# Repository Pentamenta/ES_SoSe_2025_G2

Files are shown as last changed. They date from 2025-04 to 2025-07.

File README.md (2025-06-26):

# ES_SoSe_2025_G2
 Projekt zur Entwicklung eines automatisierten Fahrzeuges und eines Dashboards für den Kurs Embedded Systems 1 an der BHT Berlin.

## Workflow

### Git

Es wird mit Git gearbeitet.  
Vor jeder Arbeitsphase wird das Repository gepullt.
Gearbeitet wird nur in Branches, niemals direkt im Main. Es wird nur gemerged, wenn der Branch erfolgreich getestet wurde.
Vor dem Commit wird ein weiteres mal gepullt, um Mergefehler durch paralleles Arbeiten zu vermeiden.

## Hardware

Als Basis für beide Projektteile wird ein Arduino Nano BLE 33 verwendet. Das Auto verfügt zusätzlich über einen Arduino MEGA, da weitere Pins für die Steuerung der IOs benötigt wurden. Der Arduino Nano BLE 33 bleicht zentrale Anlaufstelle für die Drahtloskommunikation.

Um das Board Arduino Nano BLE 33 zu bespielen:
 1. Unter Werkzeuge --> Board --> Boardverwalter wählen
 2. Nach "Arduino Mbed OS Nano Boards" suchen und installieren
 3. Unter Board erscheint nun die neue Option "Arduino Mbed OS Nano Boards"
 4. Dort "Arduino Nano 33 BLE" wählen

## Software

### Bibliotheken (Fortlaufend zu erweitern)

Für das Projekt zu installierende Bibliotheken:
- ArduinoBLE
- U8g2 von olikraus (beim Inkludieren werden 3 Bibliotheken eingefügt, wir brauchen nur die U8g2lib)
- Arduino_BMI270_BMM150
- Adafruit_SSD1306
- Adafruit_GFX
- Wire
- Servo

### Softwarestruktur

Im Repository befinden sich zwei Ordner mit darin jeweils gleichnamigen Arduino Programmen.
- Code_ Dashboard --> Code_Dashboard.ino
- Code_Car_Connect --> Code_Car_Connect.ino
- Code_Car --> Code_Car.ino

In diesen Dateien wird programmiert. Ein Aufteilen in ausgelagerte .h Dateien ist erwünscht.  

In der externen Datei EBS_BLE.h werden Variablen für die BLE Kommunikation definiert, die in allen Programmen gleich seien müssen. Aufgrund von beschränkungen der Arduino IDE kann diese Datei nicht extern verlinkt werden, sondern muss in jedem Programmordner einzeln existieren. Es ist extrem wichtig, dass diese Dateien immer auf dem selben Stand sind.

### Coding

- Es ist soviel wir möglich über Funktionen zu lösen, um den Main loop so übersichtlich wie möglich zu halten.
- Delays und längere Loops sind zu vermeiden. Das Programm muss den Loop ständig durchlaufen, um die Drahtloskpommunikation nicht zu behindern.
- Der Code ist ausführlich zu kommentieren und am Ende der Kommentare der Name des bearbeiters hinzuzufügen, um Rückfragen zu vereinfachen. Es Reicht wenn der Namen einmal zu Begin einer Funktion notiert wird.

## BLE Documentation

Die Drahtlosverbindung zwischen Dashboard und Auto wird über Bluetooth Low Energy gelöst. 
Hierbei dient das Dashboard als Central Device und das Auto als Peripheral Device.

### Einführung BLE

- Das Peripherial Device ließt Daten vom Central Device aus
	- Darunter fallen sämtliche Anweisungen an das Auto, wie zu erreichende Geschwindigkeit und Lenkeinschlag
- Das Peripherial Device schreibt Daten andas Central Device.
	- Hiermit werden laufende Daten wie Sensor - Messwerte und Geschwindigkeit an das Dashboard übergeben.

### Datenstruktur BLE im Projekt

Datenübertragung mit BLE funktioniert über sogenannte Service.
Ein Central Device stellt eine Reihe von klar Definierten Service zur verfügung. 
Das Peripherial Device, welches diesen Service kennt, kann mit dem Central Device eine Verbindung aufbauen.
Service bestehen aus so genannten Charakteristiken, welche im Endeffekt einzelne Variablen sind.
Eine Gruppe aus Service nennt man Profil.

Jeder Service besitzt eine einzigartige UUID. Entdeckt ein Peripheral Device einen Service kann dieses, die darin enthaltenen Charakteristiken, lesen, beschreiben, oder überwachen.
Jede Charakteristik besitzt ebenfalls eine einzigartige UUID.

Die Uuids un dazugehörigen Charakteristika werden in der Datei "EBS_BLE.h" deklariert. Mittels bedigter Kompilierung werden Funktionen an den jeweiligen Code angepasst.

Die Tags für die bedingte Programmierung der einzelnen Programme lauten:
- Code_Dashboard.ino --> DASH
- Code_Car_Connect.ino --> CAR_CONNECT
- Code_Car.ino --> CAR

## Features

### Fahrzeug

- Blinker / Warnlicht
- Lenkung
	- Heckantrieb mit Servolenkung vorne
- Abstandssensor mit Buzzer
- Geschwindigkeitssensor
- Tempomat

### Dashboard

- Steuerung
	- Servolenkung über Joystick
	- Gas/Bremse über Joystick
- Tacho auf Bildschirm 
- Taster für Blinker, Tempomat, Scheinwerfer
- Bildschirme (1-3): Tachoanzeige, Parkanzeige, Tempomat Geschwindigkeit, Lüfter, Heizung

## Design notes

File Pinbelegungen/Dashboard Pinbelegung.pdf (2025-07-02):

Dashboard Pinbelegung

02.07.2025

Gerät | Pin | Pin Arduino | Pin Arduino | Pin | Gerät
LED ABS | Anode | D13 | D12 | Anode | LED Airbag
- | 3V3 | 3V3 | D11 | Anode | LED Tempomat
- | - | AREF | D10 | 1 | Taster Fernlicht
Joystick links Y | 4 | A0 | D09 | 1 | SDA Bildschirm links
Joystick links X | 3 | A1 | D08 | 2 | SCL Bildschirm links
Joystick rechts Y | 4 | A2 | D07 | 1 | Taster Scheinwerfer
Joystick rechts X | 3 | A3 | D06 | 1 | Taster Tempomat Set
SDA Display mitte / rechts | 1 / 1 | A4 | D05 | 1 | Taster Tempomat An / Aus
SCL Display mitte / rechts | 2 / 2 | A5 | D04 | Anode | LED BLE Connection
LED Blinker links | Anode | A6 | D03 | 5 | Taster Joystick rechts
LED Blinker rechts | Anode | A7 | D02 | 5 | Taster Joystick links
- | - | 5V | GND | GND | -
- | - | RESET | RESET | 1 | Taster Reset
- | GND | GND | D01 | - | -
Batteriespannung | + | VIN | D00 | - | -

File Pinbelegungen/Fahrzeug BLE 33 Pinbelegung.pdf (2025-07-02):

Fahrzeug BLE 33 Pinbelegung

02.07.2025

Gerät | Pin | Pin Arduino | Pin Arduino | Pin | Gerät
- | - | D13 | D12 | - | -
- | - | 3V3 | D11 | - | -
- | - | AREF | D10 | - | -
- | - | A0 | D09 | - | -
- | - | A1 | D08 | - | -
- | - | A2 | D07 | - | -
- | - | A3 | D06 | - | -
- | - | A4 | D05 | - | -
- | - | A5 | D04 | Anode | LED BLE Connection
- | - | A6 | D03 | - | -
- | - | A7 | D02 | D04 | Arduino MEGA
- | - | 5V | GND | GND | -
- | - | RESET | RESET | - | -
- | GND | GND | D01 | D19 | Arduino MEGA Rx1
Batteriespannung | + | VIN | D00 | D18 | Arduino MEGA Tx1

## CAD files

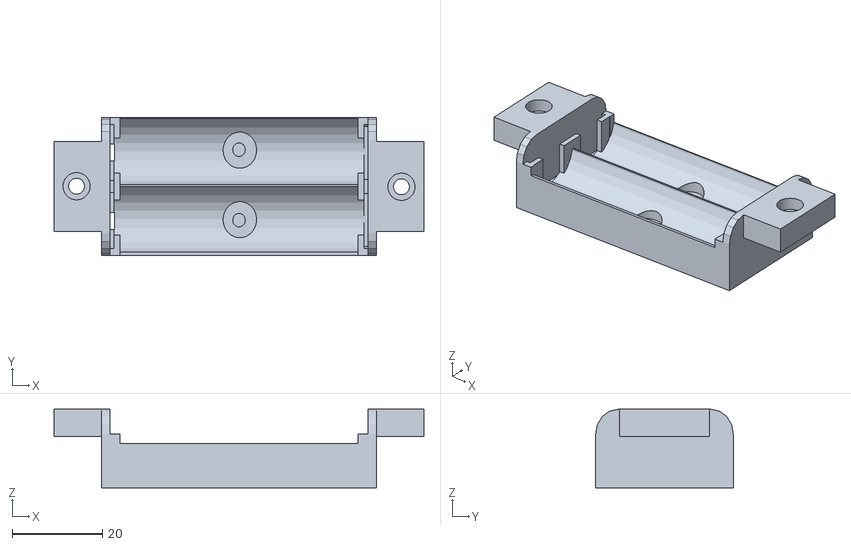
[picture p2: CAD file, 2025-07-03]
3D-Objekte/arduino 4WD controller battery holder.stl
82.0 x 30.5 x 17.4

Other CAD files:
3D-Objekte/lower_prt.prt
3D-Objekte/upper_prt.prt

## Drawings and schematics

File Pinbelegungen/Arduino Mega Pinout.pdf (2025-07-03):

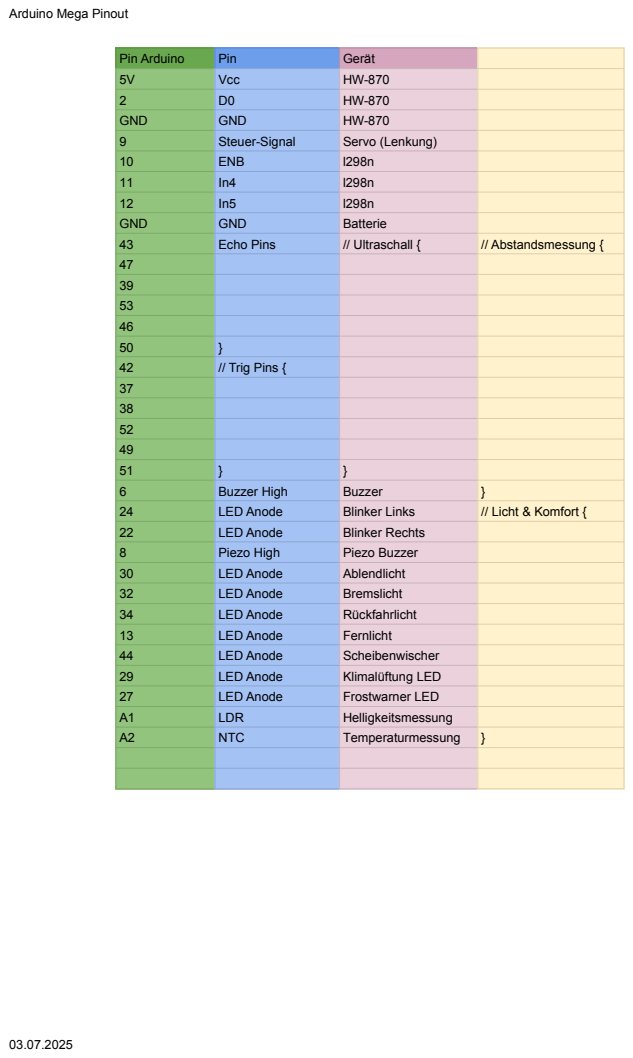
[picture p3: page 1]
Pin Arduino; Pin; Gerät; Vcc; GND; Steuer-Signal; Servo (Lenkung); ENB; Batterie; Echo Pins; // Ultraschall {; // Abstandsmessung {; // Trig Pins {; Buzzer High; Buzzer; LED Anode; Blinker Links; // Licht & Komfort {; Blinker Rechts; Piezo High; Piezo Buzzer; Ablendlicht; Bremslicht; Rückfahrlicht; Fernlicht; Scheibenwischer; Klimalüftung LED; Frostwarner LED; LDR; Helligkeitsmessung; NTC; Temperaturmessung

Arduino Mega Pinout

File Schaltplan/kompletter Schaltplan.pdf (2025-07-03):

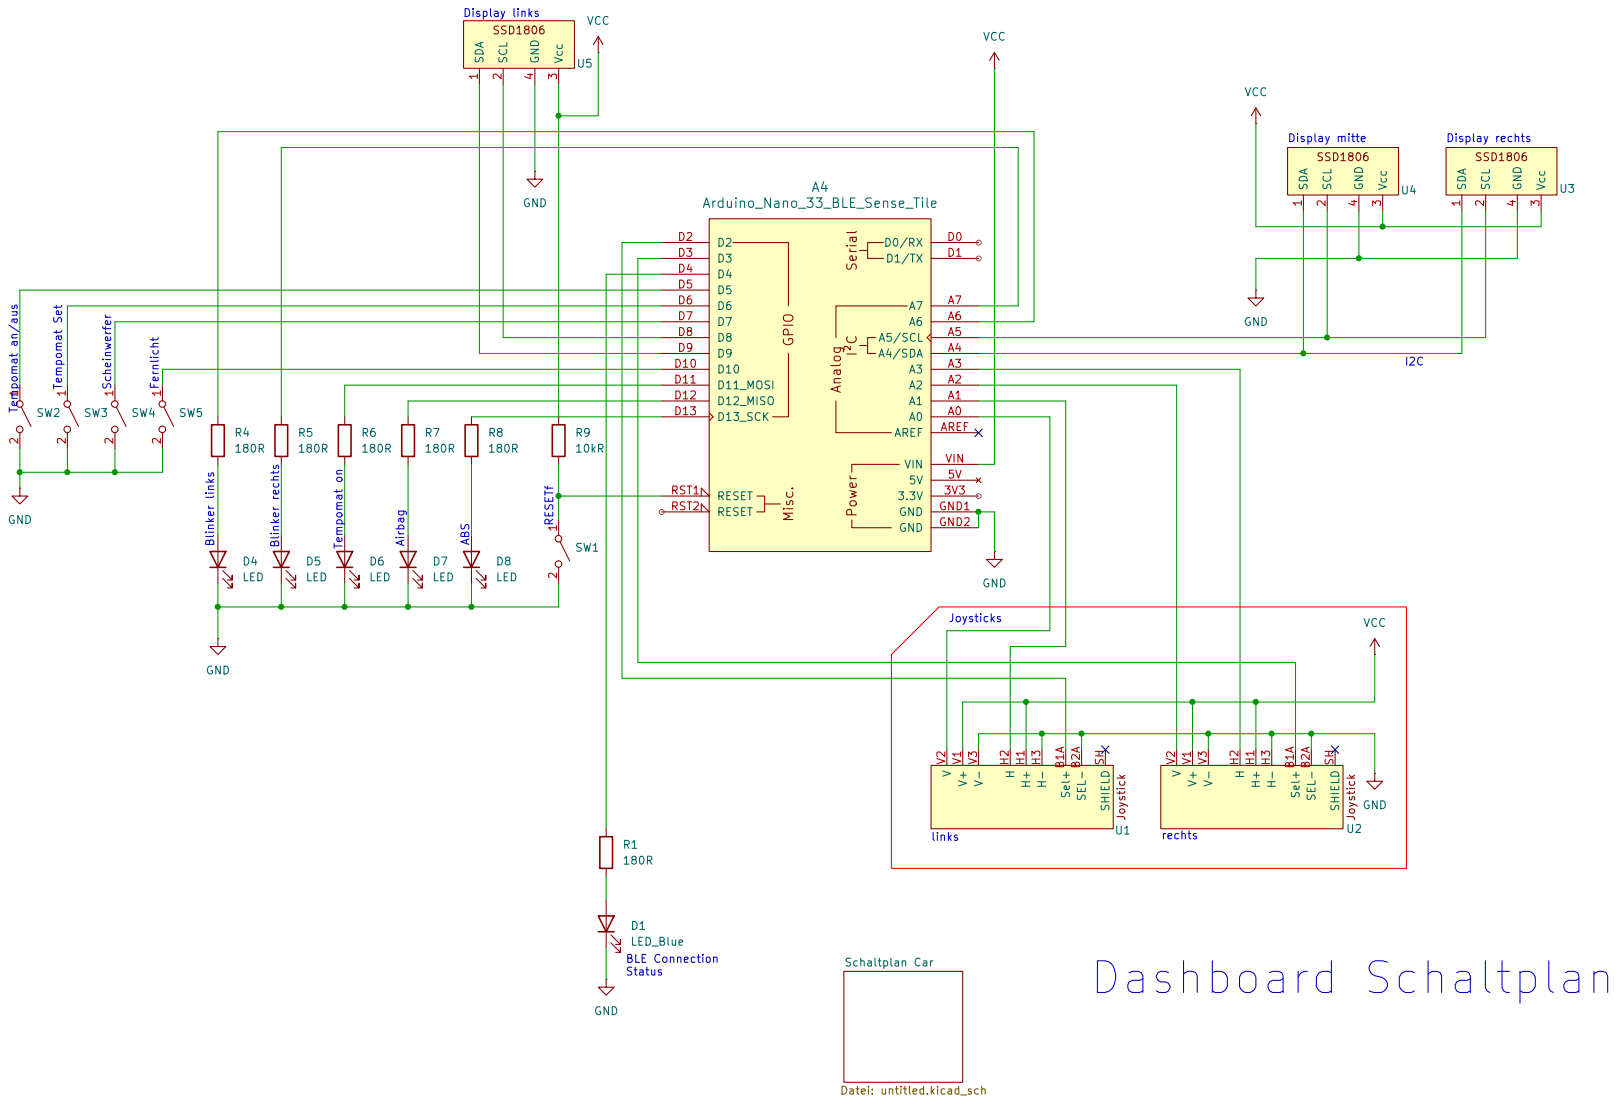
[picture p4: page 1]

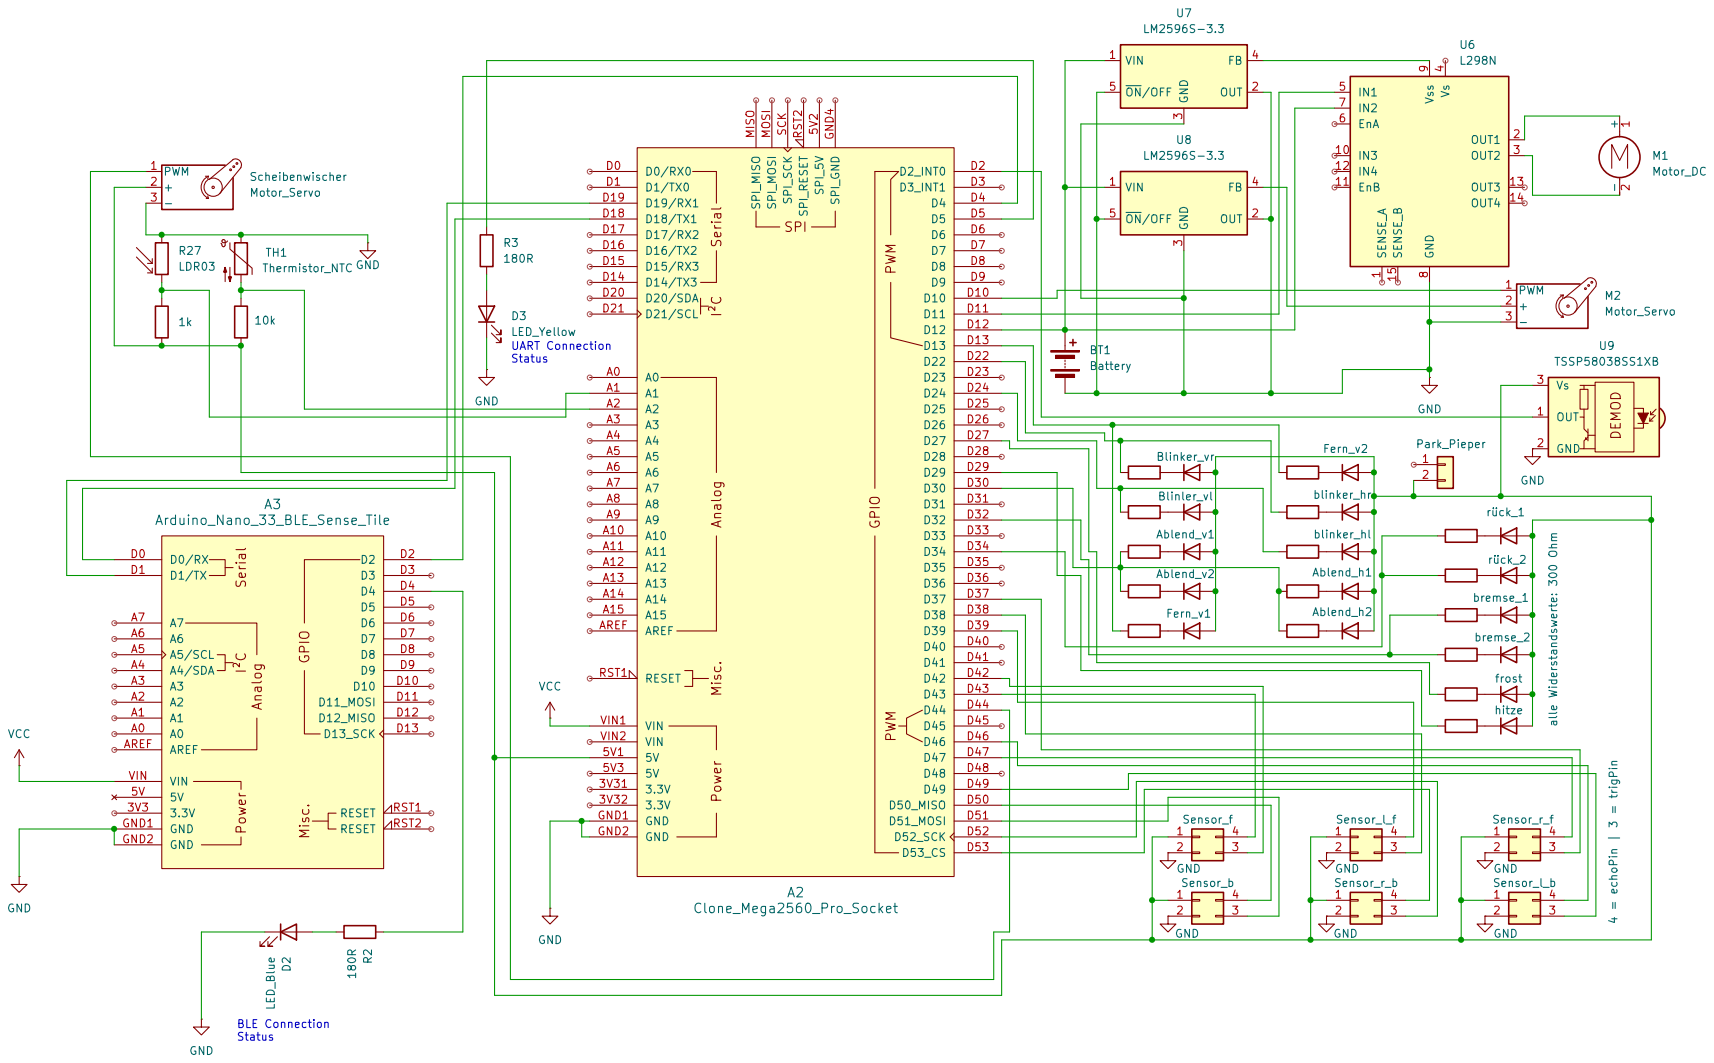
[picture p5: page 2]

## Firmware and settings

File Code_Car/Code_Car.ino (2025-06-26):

#define CAR //Flag für Precompiler (Adrian)

#include "EBS_BLE.h" //Custom Header mit BLE definitionen (Adrian)

#define CONNECT_NOTIFY 4
#define UART_LED 5

#include <HCSR04.h> // HC-SR04 Libary (Kontantin)

#include <Servo.h>  //Servo Motor Library (jan)
#define MAX_SPEED 10

//Motorsteuerung (Jan)
const int ServoAnschluss = 9;
const int ENA = 10;
const int IN1 = 11;
const int IN2 = 12;
const int MIN_PWM = 50;
float speed_target_val;
int stear_target_val;
int MotorGrad = 90;
int pwmVal;
float speed_buffer_val;
float avgSpeed = 0.0;
int speed_buffer_pwm = 0;
float speed_reg;

//Geschwindigkeitsmessung (Jan)
const byte sensorDigitalPin = 2;
volatile unsigned int pulseCount = 0;
unsigned long lastMeasurementTime = 0;
const unsigned long interval = 1000;
const float wheelCircumference = 0.305;  // Meter
float rpmValues[3] = {0, 0, 0};
float speedValues[3] = {0, 0, 0};
int index = 0;

// Abstandsmessung (Konstantin)
// Pin-Konfiguration (Reihenfolge: f, r_f, l_f, r_b, l_b, b)
const uint8_t echoPins[6] = {43, 47, 39, 53, 46, 50};
const uint8_t trigPins[6] = {42, 37, 38, 52, 49, 51};
enum SensorIndex : uint8_t { FRONT, RIGHT_FRONT, LEFT_FRONT, RIGHT_BACK, LEFT_BACK, BACK };
UltraSonicDistanceSensor* sensors[6];

// Konfiguration-Buzzer (Konstantin)
const uint8_t buzzerPin = 6;
const uint16_t BUZZER_PULSE_MS = 50;
const float MAX_VALID_DISTANCE = 300.0;

// Levelgrenzen für die Stufenberechnung (Konstantin)
const uint8_t levelThresholds[] = {10, 20, 30, 40, 50, 60};
const uint8_t LEVEL_COUNT = sizeof(levelThresholds) / sizeof(levelThresholds[0]);

Servo srv;

unsigned long t_debug;
unsigned long t_exchange;

//JJ
//aktive und passive Fahrsicherheit 

float speed = data_to_dash.speed_actual_val;       
float dps_Z = data_to_car.dps_Z_val;     
float acc_Y = data_to_car.acc_Y_val;     
float acc_Z = data_to_car.acc_Z_val;   
float angleX = data_to_car.angleX;
float angleY = data_to_car.angleY;
int16_t distance_f = data_to_dash.distance_f_val;
//Schwellwerte zur Entscheidung der Auslösechrekteristik 
const float schwelle_fahrzeug_ABS   = 0.5f;    
const float schwelle_fahrzeug_ASR   = 0.2f;    
const float schwelle_drehzahl_ASR   = 50.0f;   
const float schwelle_esp            = 30.0f;  
const float schwelle_diebstahl      = 1.5f;
const float schwelle_crash          = -0.6f;   
const float schwelle_angle_x	      = 45.0f;
const float schwelle_angle_y	      = 45.0f; 
//JJ
//Ergebnis-Flags
bool abs_active        = false;
bool asr_active        = false;
bool esp_active        = false;
bool diebstahl_active   = false;
bool airbag_active     = false;
bool ueberschlag_active = false;
bool abstand_active     = false;  

// Tamo
enum BlinkerStatus {BLINKER_NONE, BLINKER_LEFT, BLINKER_RIGHT};
BlinkerStatus lastBlinkerState = BLINKER_NONE;
BlinkerStatus currentBlinkerState = BLINKER_NONE;

#include <Servo.h>

Servo wiper;

// === Pin-Zuweisungen ===
const int joystickX = A0;    // X-Achse des Joysticks
const int joystickY = A3;    
const int leftLED = 24;       // Blinker links
const int rightLED = 22;      // Blinker rechts
const int piezoPin = 8;       // Piezo-Buzzer
const int lightSensor = A1;             // Fotowiderstand
const int Frontlicht = 30;
const int brakeLight = 32;
const int backLight = 34;    // Rückfahrlicht
const int Fernlicht = 13;
const int OnOff = 25;            // Ablendlicht
const int Warn = 23;                     // Warnblinker
const int braking = 33;          // Bremse

const int wiperPin = 44;                // Wiper
const int Wish = 31;

const int comfortBlinkerBtn = A3; // Taster für Komfortblinker

const int PIN_NTC = A2;        // Temperatur-Sensor
const int PIN_HOT = 29;         // Ausgang für Lüfter (z. B. LED oder
const int PIN_COLD = 27;          // Frostwarnung (LED oder Piezo)


// === Schwellwerte ===
const int thresholdLeft = 200;
const int thresholdRight = 800;
const int blinkDelay = 400;  // Blinkfrequenz in ms
const int toneFrequency = 440; // Tonhöhe des "Tick"
const int toneDuration = 100;  // Dauer des Tons in ms
const float R_1 = 1000.0;  // Widerstand vor Fotosensor

static unsigned long lightOffTime = 0;
static bool nachleuchten = false;

bool comfortLeftActive = false;
bool comfortRightActive = false;
int LcomfortCount = 0;
int RcomfortCount = 0;
int comfortCount = 0;
unsigned long comfortPreviousMillis = 0;

bool leftBlinkState = false;
bool rightBlinkState = false;

bool lightOn = false;
bool warningActive = false;
bool Blink = false;

//float speed_actual_val = 0;

unsigned long previousMillis = 0; //test1
unsigned long cpreviousMillis = 0; //test2

unsigned long wiperMillis = 0; //test2
bool Wip = false;
bool wishi = false;

const int linksAngle = 5;
const int rechtsAngle = 175;

unsigned long bremsPreviousMillis = 0;

int yValue;
int bValue;

const float R_REF = 10000.0;
const float T0_K = 273.15 + 25;
const float BETA = 3435;
const float R0 = 10000.0;


//Test Jan
void setup() {
Serial.begin(9600);
Serial1.begin(9600, SERIAL_8N1);

pinMode(CONNECT_NOTIFY, INPUT); // High wenn BLE Verbindung besteht (Adrian)
pinMode(UART_LED, OUTPUT); // Leuchtet wenn BLE Verbindung besteht (Adrian)

t_exchange = millis();
t_debug = millis();

//DC Motor und Servo Setup (jan)
srv.attach(ServoAnschluss, 500, 2500);
srv.write(MotorGrad);
pinMode(ENA, OUTPUT);
pinMode(IN1, OUTPUT);
pinMode(IN2, OUTPUT);

//Geschwindigkeitsmesser Setup
pinMode(sensorDigitalPin, INPUT);
attachInterrupt(digitalPinToInterrupt(sensorDigitalPin), countPulse, FALLING);

// Abstandsmessung (Konstantin)
for (uint8_t i = 0; i < 6; i++) {
sensors[i] = new UltraSonicDistanceSensor(trigPins[i], echoPins[i]);
}
// Buzzer (Konstantin)
pinMode(buzzerPin, OUTPUT);
digitalWrite(buzzerPin, LOW);

// Tamo
// — Analoge Sensoren (Fotowiderstand, Joystick, TMP36) —
pinMode(joystickX,     INPUT);        // A0
pinMode(joystickY,     INPUT);        // A3
pinMode(lightSensor,   INPUT);        // A1
pinMode(PIN_NTC,    INPUT);        // A2

// — Digitale Ausgänge (LEDs, Piezo, Motoren) —
pinMode(leftLED,       OUTPUT);       // D4
pinMode(rightLED,      OUTPUT);       // D2
pinMode(piezoPin,      OUTPUT);       // D8
pinMode(Frontlicht,    OUTPUT);       // D10 (PWM)
pinMode(brakeLight,    OUTPUT);       // D12
pinMode(Fernlicht,     OUTPUT);       // D13
pinMode(wiperPin,    OUTPUT);       // D11 (PWM)
pinMode(PIN_HOT,    OUTPUT);       
pinMode(PIN_COLD,      OUTPUT);      

// — Digitale Eingänge mit internem Pull-Up (Buttons/Taster) —
pinMode(OnOff,               INPUT_PULLUP); // D7  Licht-Taster
pinMode(Warn,                INPUT_PULLUP); // D6  Warnblinker-Taster
pinMode(braking,             INPUT_PULLUP); // D5  Bremspedal-Taster
pinMode(Wish,         INPUT_PULLUP); // D31  Wischer-Taster
pinMode(comfortBlinkerBtn,   INPUT_PULLUP); // A3 Komfortblinker-Taster

wiper.attach(wiperPin);
}

void loop() {
//jan 
handleSteering();   // Servo Motor
handleDrive();      // DC Motor
handleRPMandSpeed(); //RPM Messung
buffer();

//JJ
abs_active        = checkABS(pulseCount ,  speed, schwelle_fahrzeug_ABS);
asr_active        = checkASR(speed, pulseCount, schwelle_drehzahl_ASR, schwelle_fahrzeug_ASR);
esp_active        = checkESP( dps_Z, schwelle_esp);
diebstahl_active   = checkDiebstahl( acc_Z,schwelle_diebstahl);
airbag_active      = checkAirbag(acc_Y, schwelle_crash );
ueberschlag_active = checkAbstand(distance_f,speed);
abstand_active     = checkAbstand(distance_f,speed); 

boolean_to_dash_arr[0][10]= abs_active;
boolean_to_dash_arr[0][11]= ueberschlag_active;
boolean_to_dash_arr[0][12]= diebstahl_active;
boolean_to_dash_arr[0][13]= airbag_active;
boolean_to_dash_arr[0][14]= esp_active;
boolean_to_dash_arr[0][15]= asr_active;
boolean_to_dash_arr[1][0]= abstand_active;


if (digitalRead(CONNECT_NOTIFY)) {
  digitalWrite(UART_LED, HIGH);
}
else {
  digitalWrite(UART_LED, LOW);
}


if (millis() >= t_exchange + 20) { // BLE und Serial Kommunikation (Adrian)
  package_bool();
  Serial_val_exchange();
  unpack_bool();
  t_exchange = millis();
  }

if (millis() >= t_debug + 500){ // Debug Loop
  //Serial.println("Bin im Main");

  //Debug_data();
  //Serial.print("To Car: ");
  //Serial.println(sizeof(data_to_car));
  //Serial.print("To Dash: ");
  //Serial.println(sizeof(data_to_dash));

  t_debug = millis();
  }
// Abstandsmessung (Konstantin)
// Messwerte aktualisieren und direkt in vorhandene Variablen schreiben
float current;
current = sensors[FRONT]->measureDistanceCm();
data_to_dash.distance_f_val = getDistanceLevel(current);

current = sensors[BACK]->measureDistanceCm();
data_to_dash.distance_b_val = getDistanceLevel(current);

current = sensors[RIGHT_FRONT]->measureDistanceCm();
data_to_dash.distance_r_f_val = getDistanceLevel(current);

current = sensors[RIGHT_BACK]->measureDistanceCm();
data_to_dash.distance_r_b_val = getDistanceLevel(current);

current = sensors[LEFT_FRONT]->measureDistanceCm();
data_to_dash.distance_l_f_val = getDistanceLevel(current);

current = sensors[LEFT_BACK]->measureDistanceCm();
data_to_dash.distance_l_b_val = getDistanceLevel(current);

// Parkstatus in globales Array speichern
boolean_to_car_arr[0][9] = isParkingFree(data_to_dash.distance_l_f_val, data_to_dash.distance_l_b_val);
boolean_to_car_arr[0][8] = isParkingFree(data_to_dash.distance_r_f_val, data_to_dash.distance_r_b_val);

// Buzzer abhängig von Rücksensor
updateBuzzer(data_to_dash.distance_b_val);

// Tamo

unsigned long currentMillis = millis(); //test1
unsigned long comfortMillis = millis(); //test1

int xValue = analogRead(joystickX);
int yValue = analogRead(joystickY);
   
   

int y = analogRead(lightSensor); // ADC = y
float U_light = y * (5.0 / 1023.0);
float R_light = U_light / (5.0 - U_light) * R_1;

int ledBrightness = map(y, 0, 1023, 0, 255); // Umrechnen!

// === Temperaturmessung über TMP36 ===
//int sensorValue = analogRead(tempSensor);
//float voltage = sensorValue * (5.0 / 1023.0); // Spannung in Volt
//float temperatureC = (voltage - 0.5) * 100.0; // Temperatur in °C

     
// === Temperaturmessung über NTC ===
int raw = analogRead(PIN_NTC);  // 0–1023
float Vout = raw * (5.0 / 1023.0);
// Berechne NTC-Widerstand: Rntc = R_ref * Vout / (Vcc - Vout)
float Rntc = R_REF * Vout / (5.0 - Vout);
    
// 1/T = 1/T0 + (1/BETA) * ln(Rntc/R0)
float invT = (1.0 / T0_K) + (1.0 / BETA) * log(Rntc / R0);
float T_K = 1.0 / invT;         // Temperatur in Kelvin
float T_Craw = T_K - 273.15;      // Temperatur in °C
float T_C = T_Craw + 16;      // Fehelrkorektur

Serial.println(T_C);
Serial.println(digitalRead(PIN_HOT));

data_to_dash.temperature_val = T_C;
 

// === Klimaentlüftung einschalten bei > 25 °C ===
if (T_C > 27.0) {
  digitalWrite(PIN_HOT, HIGH);
} else {
  digitalWrite(PIN_HOT, LOW);
}

// === Frostwarner aktivieren bei < 4 °C ===
if (T_C < 4.0) {
  digitalWrite(PIN_COLD, HIGH);
    //tone(8, 1000, 200); // Piezo auf Pin 8 (wenn angeschlossen)
} else {
  digitalWrite(PIN_COLD, LOW);
   }


   

  // Bremslicht (yValue < 500) && (yValue > 150)
   if (boolean_to_car_arr[0][5] || digitalRead(braking)) {
     analogWrite(brakeLight, 255); // sehr helles Bremslicht
     boolean_to_dash_arr[0][5] = true;
   } else {
     analogWrite(brakeLight, 0);
     boolean_to_dash_arr[0][5] = true;
   }

   // bValue = yValue;

   // Rückfahrtlicht
   if (data_to_car.speed_target_val < 0 || yValue < 250) {
     analogWrite(backLight, 255);
   } else {
     analogWrite(backLight, 0);
   }

   // Warnblinker taster
   if (digitalRead(Warn)  == true) {
     boolean_to_car_arr[0][2] = !boolean_to_car_arr[0][2];
     digitalWrite(leftLED, false);
     digitalWrite(rightLED, false);
     delay(200);
   }
   // Warnblinker
   if (boolean_to_car_arr[0][2]) {
     boolean_to_dash_arr[0][2] = true;
     if (currentMillis - previousMillis >= blinkDelay) {
       previousMillis = currentMillis;
          Blink = !Blink;
       digitalWrite(leftLED, Blink);
       digitalWrite(rightLED, Blink);
       if (Blink) {
         tone(piezoPin, toneFrequency, toneDuration);
       }
     }
   } else {
    boolean_to_dash_arr[0][2] = false;
   }

   // Ablendlicht Taster
   if (digitalRead(OnOff) == true) {
     boolean_to_car_arr[0][3] = !boolean_to_car_arr[0][3];
     delay(200);
     if (!boolean_to_car_arr[0][3]) {
       nachleuchten = true;
          lightOffTime = millis();
        }
   }
   // Ablendlicht
    if (boolean_to_car_arr[0][3] == true) {
      analogWrite(Frontlicht, ledBrightness); // Helligkeit steuern
      boolean_to_dash_arr[0][3] = true;

        // Fernlicht
        if (y > 900) {
        analogWrite(Fernlicht, 255);
        boolean_to_dash_arr[0][4] = true;
        } else {
        analogWrite(Fernlicht, 0);
        boolean_to_dash_arr[0][4] = false;
        }

      lightOffTime = millis();
   } else {
     if (millis() - lightOffTime < 5000) {  //Wegbeleuchtung
      analogWrite(Frontlicht, ledBrightness);
     } else {
      analogWrite(Frontlicht, 0); // Helligkeit aus
      analogWrite(Fernlicht, 0);
      boolean_to_dash_arr[0][3] = false;
     }
   }

   // Komfortblinker
   if (boolean_to_car_arr[0][1] || xValue < thresholdLeft) {
     currentBlinkerState = BLINKER_LEFT;
   } else if (boolean_to_car_arr[0][0] || xValue > thresholdRight) {
     currentBlinkerState = BLINKER_RIGHT;
   } else {
     currentBlinkerState = BLINKER_NONE;
   }

  if (currentBlinkerState != lastBlinkerState) {
   if (lastBlinkerState == BLINKER_LEFT) LcomfortCount = 6;
   else if (lastBlinkerState == BLINKER_RIGHT) RcomfortCount = 6;
   lastBlinkerState = currentBlinkerState;
  }

  if (comfortMillis - cpreviousMillis >= blinkDelay) {
    cpreviousMillis = currentMillis;
    RcomfortCount -= 1;
    LcomfortCount -= 1;

  }

   // Blinker links
   if (boolean_to_car_arr[0][1] || (LcomfortCount > 0) || xValue < thresholdLeft) {
     digitalWrite(rightLED, false);
     boolean_to_dash_arr[0][1] = true;
     if (currentMillis - previousMillis >= blinkDelay) {
       previousMillis = currentMillis;
          Blink = !Blink;
       digitalWrite(leftLED, Blink);
       if (Blink == true) {
         tone(piezoPin, toneFrequency, toneDuration);
       }
     }
     boolean_to_dash_arr[0][0] = false;
   }

   // Blinker rechts
   else if (boolean_to_car_arr[0][0] || (RcomfortCount > 0) || xValue > thresholdRight) {
     digitalWrite(leftLED, false);
     boolean_to_dash_arr[0][0] = true;
     if (currentMillis - previousMillis >= blinkDelay) {
       previousMillis = currentMillis;
          Blink = !Blink;
       digitalWrite(rightLED, Blink);
       if (Blink == true) {
         tone(piezoPin, toneFrequency, toneDuration);
       }
     }
     boolean_to_dash_arr[0][1] = false;
   }
   // Zentriert → alles aus
   else if (boolean_to_car_arr[0][2] == false) {
     digitalWrite(leftLED, LOW);
     digitalWrite(rightLED, LOW);
     noTone(piezoPin); // Sicherheitshalber abschalten
     //Serial.println(comfortCount);
      boolean_to_dash_arr[0][0] = false;
      boolean_to_dash_arr[0][1] = false;
   }
   
   if (digitalRead(Wish) == true) {
     boolean_to_car_arr[1][1] = !boolean_to_car_arr[1][1];
     delay(200);
   }

    if(boolean_to_car_arr[1][1]){
      boolean_to_dash_arr[1][1] = true;
      if (currentMillis - wiperMillis >= 1000) {
        wiperMillis = currentMillis;
            Wip = !Wip;
        if (Wip == true) {
          wiper.write(rechtsAngle);
        } else {
          wiper.write(linksAngle);
        }
      }
    } else {
      boolean_to_dash_arr[1][1] = false;
    }
}


void countPulse() {
  pulseCount++;
}

//buffer
void buffer() {
  speed_buffer_val = data_to_car.speed_target_val;
  float error = speed_buffer_val - avgSpeed;
  const float KP = 100.0;
  speed_buffer_pwm = constrain(error * KP, -255, 255);
}

//jan
void handleSteering() {
  int xVal;
  if(digitalRead(CONNECT_NOTIFY)){
  xVal = data_to_car.stear_target_val;
  }
  else{ xVal = 0;
  }

  if (xVal > -5 && xVal < 5) {
    MotorGrad = 90; // Zentrum
  } else if (xVal <= -5) {
    MotorGrad = map(xVal, -5, -100, 90, 40); // Links
  } else if (xVal >= 5) {
    MotorGrad = map(xVal, 5, 100, 90, 140); // Rechts
  }
  srv.write(MotorGrad);
  
  data_to_dash.stear_actual_val = xVal;
}

//jan
void handleDrive() {
  
  if(digitalRead(CONNECT_NOTIFY)){
  int pwmVal = speed_buffer_pwm;
  }
  else{int pwmVal = 0;}

   

  if (speed_buffer_pwm > 0.0) {
    // Vorwärts
    digitalWrite(IN1, HIGH);
    digitalWrite(IN2, LOW);
    analogWrite(ENA, max(pwmVal, MIN_PWM));
  }
  else if (speed_buffer_pwm < 0.0) {
    // Rückwärts
    digitalWrite(IN1, LOW);
    digitalWrite(IN2, HIGH);
    analogWrite(ENA, max(-pwmVal, MIN_PWM));
  }
  else {
    // Stop
    digitalWrite(IN1, LOW);
    digitalWrite(IN2, LOW);
    analogWrite(ENA, 0);
  }
}

//jan
void handleRPMandSpeed() {
  unsigned long currentTime = millis();

  if (currentTime - lastMeasurementTime >= interval) {
    detachInterrupt(digitalPinToInterrupt(sensorDigitalPin));

    float currentRPM = pulseCount * 60.0;

    // Direkt in m/s berechnen
    float currentSpeed = (pulseCount * wheelCircumference) / (interval / 1000.0);  // m/s

    // Alternativ mit RPM (zur besseren Lesbarkeit):
    // float currentSpeed = (currentRPM / 60.0) * wheelCircumference;

    rpmValues[index] = currentRPM;
    speedValues[index] = currentSpeed;
    index = (index + 1) % 3;

    float avgRPM = (rpmValues[0] + rpmValues[1] + rpmValues[2]) / 3.0;
    float avgSpeed = (speedValues[0] + speedValues[1] + speedValues[2]) / 3.0;

    pulseCount = 0;
    lastMeasurementTime = currentTime;

    attachInterrupt(digitalPinToInterrupt(sensorDigitalPin), countPulse, FALLING);

    data_to_dash.speed_actual_val = avgSpeed;  // Jetzt direkt in m/s
  }
}


//JJ aktive passive sicher heit -> bool Fuktionen

// ABS: Rad blockiert, wenn Fahrzeug schnell genug und Raddrehzahl = 0
bool checkABS(volatile unsigned int pulseCount , float speed, float schwelle_fahrzeug_ABS) 

  {
    float currentRPM = pulseCount * 60.0f;
  return (speed> schwelle_fahrzeug_ABS) && (currentRPM == 0.0f);
  }
  
  

// ASR: Antriebsschlupf, wenn Fahrzeug langsam und Räder zu schnell
bool checkASR(float speed,volatile unsigned int pulseCount, float schwelle_drehzahl_ASR, float schwelle_fahrzeug_ASR) 
{
  float currentRPM = pulseCount * 60.0;
  return ( speed < schwelle_fahrzeug_ASR  && currentRPM > schwelle_drehzahl_ASR);

}

// ESP: Schleudern erkannt, wenn Z-Gyro > Schwelle
bool checkESP(float dps_Z, float schwelle_esp) 
{
  return (abs( dps_Z) > schwelle_esp);
}

// Diebstahl: Anheben erkannt, wenn Z-Beschleunigung < -Schwelle
bool checkDiebstahl(float acc_Z, float schwelle_diebstahl)
{
  return (acc_Z <= schwelle_diebstahl );
}


// Airbag: Crash erkannt, wenn Y-Beschleunigung < Schwelle
bool checkAirbag(float acc_Y, float schwelle_crash ) 
{
  return (acc_Y <   schwelle_crash  );
}

// Überschlag: erkannt, wenn angleX oder angleY > Schwelle
bool checkUeberschlag(float angleX,float angleY , float schwelle_angle_y,float schwelle_angle_x) 
{
  return (abs(angleX) >= schwelle_angle_x || abs(angleY) >= schwelle_angle_y);
}

// kritischer Abstand: erkannt, wenn Abstand vorne < dynamische Schwelle
bool checkAbstand(int16_t distance_f, float speed) 
{ 
//Schwelle für Abstand – wird dynamisch berechnet
 float schwelle_abstand = ( speed * 100.)/2;

  return (distance_f < schwelle_abstand);
}

// Stufenberechnung (Konstantin)
uint8_t getDistanceLevel(float d) {
  if (isnan(d) || d < 0 || d > MAX_VALID_DISTANCE) return 255;
  for (uint8_t i = 0; i < LEVEL_COUNT; i++) {
    if (d < levelThresholds[i]) return i;
  }
  return 255;
}

// Parklückenerkennung (Konstantin)
bool isParkingFree(uint8_t level1, uint8_t level2) {
  return !(level1 == 0 || level1 == 1 || level2 == 0 || level2 == 1);
}

// Pieper-Intervall (Konstantin)
unsigned long getBeepInterval(uint8_t level) {
  return (level < LEVEL_COUNT) ? 100 + level * 200 : 0;
}

// Pieper (Konstantin)
void updateBuzzer(uint8_t level) {
  static unsigned long lastBeepTime = 0;
  static bool buzzerState = false;
  static unsigned long beepStartTime = 0;

  unsigned long now = millis();
  unsigned long interval = getBeepInterval(level);

  if (interval > 0) {
    if (!buzzerState && now - lastBeepTime >= interval) {
      digitalWrite(buzzerPin, HIGH);
      buzzerState = true;
      beepStartTime = now;
      lastBeepTime = now;
    }
    if (buzzerState && now - beepStartTime >= BUZZER_PULSE_MS) {
      digitalWrite(buzzerPin, LOW);
      buzzerState = false;
    }
  } else {
    digitalWrite(buzzerPin, LOW);
    buzzerState = false;
  }
}

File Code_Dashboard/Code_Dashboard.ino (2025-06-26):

#define DASH //Flag für Precompiler (Adrian)

#define BLE_LED 4
#define MAX_SPEED 10  // m/s
#define MAX_STEAR 100 // Ausschlag zum Steuern

// Tempomat
float tempo_speed = 0;      // Tempomat Geschwindigkeit
bool tempo_on = false;  // Ist der Tempomat an?

#include <ArduinoBLE.h> 
#include "EBS_BLE.h"  // Custom Header mit BLE definitionen (Adrian)
#include "Joystick.h" // Custom Header mit Joystick Funktionen (Adrian)
#include "Buttons.h"  // Custom Header für Button Anfrage (Adrian)
#include "Leds.h"
#include <U8g2lib.h> //Software I2C Display Ansteuerung (Eva)
#include <math.h>    //für Grafiken auf Displays (Eva)


unsigned long t_debug, t_fast, t_slow;

// Einbinden der Bibliotheken für I2C-Kommunikation und Display-Ansteuerung
#include <Wire.h>                   // Für I2C-Kommunikation
#include <Adafruit_GFX.h>           // Grundlegende Grafikfunktionen (Text, Linien etc.)
#include <Adafruit_SSD1306.h>       // Treiber für SSD1306 OLED-Display

// Konstante Maße des Displays
const int SCREEN_WIDTH = 128;       // Breite in Pixel
const int SCREEN_HEIGHT = 64;       // Höhe in Pixel

// Erstellen des Displayobjekts über I2C-Verbindung
Adafruit_SSD1306 display(SCREEN_WIDTH, SCREEN_HEIGHT, &Wire, -1);

//Software I2C Pininitialisierung (Eva) für linkes Display, R3 für die Displaydrehung
//U8G2_SSD1306_128X64_NONAME_F_SW_I2C ldisplay(U8G2_R3, /* clock=*/ 8, /* data=*/ 9, /* reset=*/ U8X8_PIN_NONE);

#include "Tacho.h" //Einbindung der Funktionen/Variablen für mittleres Display: Tache & Tempomat (Shari)
#include "Abstandsmessung.h" //Einbindung der Funktionen/Variablen zur Abstandsmessung (Shari)
//#include "leftDisplay.h" //Einbindung der Funktionen/Variablen für linkes Display: Tempomat (Eva)

unsigned long t_exchange;

// Variablen zur Abstandsmessung
void setup() {
Serial.begin(9600);
//while(!Serial); // Nur für Debug Zwecke verwenden
t_debug, t_fast, t_slow = millis();

pinMode(BLE_LED, OUTPUT);
Led_Setup();
joystick_setup(); // Initialisiert Joysticks (Adrian)
Button_Setup();
//ldisplay.begin();

// Ausgabe des Dysplays 3D über I2C (Shari)
 if (!display.begin(SSD1306_SWITCHCAPVCC, 0x3D)) {
    Serial.println(F("SSD1306 allocation failed")); // Fehlerausgabe, wenn das Dysplay nicht erkannt wird
    while (true); // Endlosschleife bei Fehler
  }
  abstand(data_to_dash.distance_f_val, data_to_dash.distance_l_f_val, data_to_dash.distance_r_f_val, data_to_dash.distance_b_val, data_to_dash.distance_l_b_val, data_to_dash.distance_r_b_val, boolean_to_dash_arr[0][9], boolean_to_dash_arr[0][8], boolean_to_dash_arr[0][3], boolean_to_dash_arr[0][4], boolean_to_dash_arr[0][7], boolean_to_dash_arr[0][6]);

//Ausgabe der Dysplays 3C über I2C (Shari)
  if(!display.begin(SSD1306_SWITCHCAPVCC, 0x3C)) { // Address 0x3C for 128x64
    Serial.println(F("SSD1306 allocation failed")); // Fehlerausgabe, wenn das Dysplay nicht erkannt wird
    while (true); // Endlosschleife bei Fehler;
  }
 tachorech(); // Skalenpunkte vorberechnen

BLE_Setup(); //Öffnet die BLE-Schnittstelle und initiallisiert das Central Device (Adrian)
connect_car(); //Stellt Verbindung mit dem Auto her (Adrian)

}

void loop() {

  if (!car.connected()) { // Stellt Verbindung wieder her (Adrian)
    // Anzeige auf dem Bildschirm
    // Fahrzeug Steuerung resetten
    connect_car();
  }

  if (millis() >= t_fast + FAST_CYCLE) { // schnelle BLE und Serial Kommunikation (Adrian)
    data_to_car.stear_target_val = read_stear();
    BLE_fast_exchange();
    writeTacho(data_to_dash.speed_actual_val, tempo_speed, tempo_on, data_to_dash.temperature_val, angleY); 
    t_fast = millis();
  }

  // Funktionen Tasterabfrage + LEDs
  Led_Update();
  speed_control();
  button_eval();


  if (millis() >= t_slow + SLOW_CYCLE) { // langsame BLE Kommunikation (Adrian)
    BLE_slow_exchange();
    t_slow = millis();
  }

  if (millis() >= t_debug + 500){ // Debug Loop
    //Serial.println("Bin im Main");
    //Debug_data();
    //joystick_debug();
    t_debug = millis();
  }

  //writedispl(speed_actual_val);

}

float read_speed() { // Ließt linken Joystick für Beschleunigung aus (Adrian)

int buffer = read_joystick_pos(1);
float max = MAX_SPEED;
float dead = DEADZONE_LOWER;

float speed = (max/dead)*buffer;
return -speed;

}

float read_stear() { // Ließt rechten Joystick für Lenkung aus (Adrian)

int buffer = read_joystick_pos(2);
float max = MAX_STEAR;
float dead = DEADZONE_LOWER;

float stear = (max/dead)*buffer;
return stear;

}

void speed_control() {

  if (tempo_on && (read_speed() <= tempo_speed) && (read_speed() >= 0)) {
    data_to_car.speed_target_val = tempo_speed;
  }
  else if (tempo_on && (read_speed() > tempo_speed) && (read_speed() >= 0)) { // Tempomat ist an und es wird beschleunigt
    data_to_car.speed_target_val = read_speed();
  }
  else if (tempo_on && (read_speed() < 0)) { // Beim bremsen geht der Tempomat aus
    tempo_on = false;
    data_to_car.speed_target_val = read_speed();
  }
  else { // Tempomat ist aus
      data_to_car.speed_target_val = read_speed();
  }

}

void button_eval() {

  // Button 1 - Tempomat on
  if (t1 && !tempo_on) {  // Einschalten
    tempo_speed = data_to_dash.speed_actual_val; // Tempomat Geschwindigkeit auf aktuellen Wert setzen
    tempo_on = true;      // Tempomat einschalten
    t1 = false;           // Button resetten
  }
  else if (t1 && tempo_on) {
    tempo_on = false;     // Tempomat auschalten
    t1 = false;           // Button resetten
  }

  // Button 2 - Tempomat set
  if (t2 && !tempo_on) {  // Einschalten
    if (tempo_speed == 0) {
      // Tempomat Geschwindigkeit auf aktuellen Wert setzen, falls noch nicht gesetzt
      tempo_speed = data_to_dash.speed_actual_val; 
    }
    tempo_on = true;      // Tempomat einschalten
    t2 = false;           // Button resetten
  }
  else if (t2 && tempo_on) { // Tempomat auf aktuellen speed setzen
    tempo_speed = tempo_speed = data_to_dash.speed_actual_val;
    t2 = false;           // Button resetten
  }

  // Button 3 - Licht
  if (t3) {
    // Scheinwerfer toggeln
    boolean_to_car_arr[0][3] = !boolean_to_car_arr[0][3];
    t3 = false;
  }

  // Button 4 - Fernlicht
    if (t4 && boolean_to_dash_arr[0][3]) {
    // Fernlicht toggeln
    boolean_to_car_arr[0][4] = !boolean_to_car_arr[0][4];
    t4 = false;
  }

  // Joystick Buttons - Blinker
  if (jl_sw && jr_sw) { // Beide Taster Gleichzeitig --> Warnblinker
    boolean_to_car_arr[0][2] = !boolean_to_car_arr[0][2];
    jl_sw, jr_sw = false;
  }
  else if (jl_sw && !jr_sw) { // Blinker links
    boolean_to_car_arr[0][1] = !boolean_to_car_arr[0][1];
    jl_sw = false;
  }
  else if (!jl_sw && jr_sw) { // Blinker rechts
    boolean_to_car_arr[0][0] = !boolean_to_car_arr[0][0];
    jr_sw = false;
  }
}

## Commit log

2025-04-17 added scemati and custom library
    [ES_SoSe_25_Schaltplan.kicad_pcb, ES_SoSe_25_Schaltplan.kicad_sch]
2025-04-22 updated scematic
    [ES_SoSe_25_Schaltplan.kicad_sch]
2025-04-24 updated readme and fixed car programm
    [Code_Car.ino]
2025-04-24 added BLE LED
    [ES_SoSe_25_Schaltplan.kicad_sch, untitled.kicad_sch]
2025-05-09 started UART
2025-05-11 finsished UART Sender
2025-05-13 made progress with UART
2025-05-14 uart barebones works
2025-05-16 finalysed uart
2025-05-17 updated scematic and added UART LED
    [ES_SoSe_25_Schaltplan.kicad_sch, untitled.kicad_sch]
2025-05-17 fixed major errors in uart
    [Code_Car.ino, Code_Car_Connect.ino, Code_Dashboard.ino]
2025-05-22 adjusted scematic
    [ES_SoSe_25_Schaltplan.kicad_sch]
2025-05-22 software_I2C_display
    - readme änderung
    - funktion zur anzeige eines uint16_t Werts auf einem Display per software implenentiertem I2C
2025-05-22 Update Readme
    Anmerkung zur Installation der Bibliothek U8g2
2025-06-11 Motor und H-Brücke im Schaltplan eingefügt
    [ES_SoSe_25_Schaltplan.kicad_sch, untitled.kicad_sch]
2025-06-12 gyroscope implemented
2025-06-12 added temperature val
2025-06-13 changed mega pins
    [ES_SoSe_25_Schaltplan.kicad_sch, untitled.kicad_sch]
2025-06-13 updated uart
2025-06-16 changed to periperal device handler
2025-06-18 edited ble and scematic
    [ES_SoSe_25_Schaltplan.kicad_sch]
2025-06-19 Added SERVO DC RPM
2025-06-19 implemented buttons
2025-06-19 implemented buttons as interrupts
2025-06-20 led rewrite
2025-06-21 stearing range angepasst von -10 bis 10 und Rückgabe geaddet.
2025-06-21 edited scematic
    [ES_SoSe_25_Schaltplan.kicad_sch]
2025-06-23 implemented temperature
2025-06-23 temperature now send to car
2025-06-24 Revert "Merge branch 'main' of https://github.com/Pentamenta/ES_SoSe_2025_G2"
    This reverts commit 633f44c77367f397391485cb5a8d936b1da149da, reversing
    changes made to 5d90c5d559d61074f78ab075b0e5420bf00b6904.
    [Buttons.h, Code_Car.ino, Code_Car_Connect.ino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]
2025-06-24 Revert "Display"
    This reverts commit 5d90c5d559d61074f78ab075b0e5420bf00b6904.
    [Code_Dashboard.ino, Tacho.h]
2025-06-24 edited out temperature sensor
2025-06-25 Update Code_Car.ino
    einfügen aller relevanten code abschnitte für aktive und passive Fahrsicherheit
2025-06-26 removed Debug prints
2025-06-30 Schaltplan Vollständig Jan
    [ES_SoSe_25_Schaltplan.kicad_sch, untitled.kicad_sch]
2025-07-02 resorted files
    [ES_SoSe_25_Schaltplan.kicad_pcb, ES_SoSe_25_Schaltplan.kicad_sch, untitled.kicad_sch]
2025-07-03 added 3dfiles
    [arduino 4WD controller battery holder.stl, lower_prt.prt, upper_prt.prt]
2025-07-03 added pin mapping
    [arduino 4WD controller battery holder.stl, lower_prt.prt, upper_prt.prt]
